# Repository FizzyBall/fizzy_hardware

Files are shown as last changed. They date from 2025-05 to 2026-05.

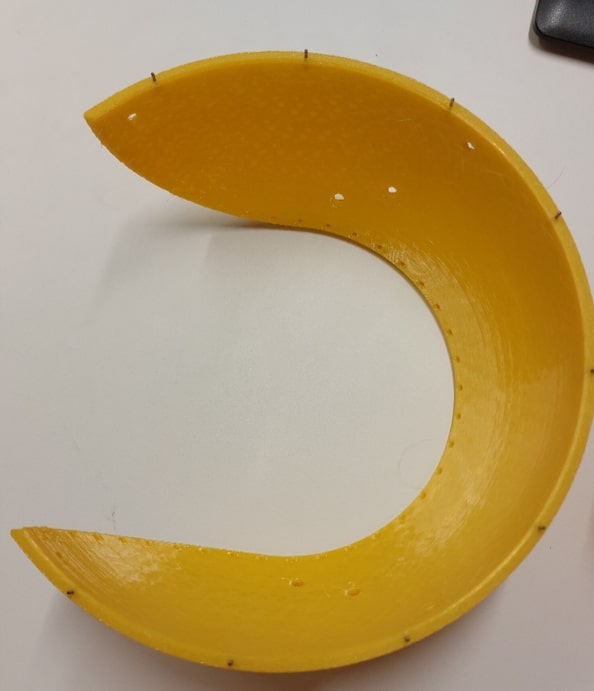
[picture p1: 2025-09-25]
Fizzy_BOM_pictures/image028.jpg

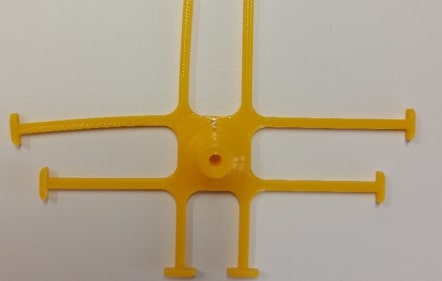
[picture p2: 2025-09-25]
Fizzy_BOM_pictures/image029.jpg

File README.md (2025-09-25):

# Hardware
Embodiment of the robotic ball

Assemblyv22-ezgif com-video-to-gif-converter

Drivetrain V3.0


Drivetrain V3.1


Rigid shell V1


Rigid shell V2


Flexible shell V1


Flexible shell V2


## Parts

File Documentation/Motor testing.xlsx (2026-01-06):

Requirements | min | max | unit | Setup | Voltage (V) | Stall torque (Nm) | Stall current (A) | Speed (RPM) | Mechanical power (W) | Electrical power (W) | Speed Counter Clockwise | No Load Current | Comments
Rotating Mass | 0.15 | 0.2 | kg | TS90M
Distance rotating mass to center of rotation | 0.035 | 0.045 | m | With PCB and battery | 5 | 0.22 | - | 114 | 1.29 | - | 112 | - | Speed with load 75 (clockwise) 67 (counterclockwise)
Torque to hold the drivetrain horizontal | 0.052 | 0.088 | Nm | With PCB and power supply | 5 | 0.20 | 1.2 | 115 | 1.20 | 6 | 109 | 0.356 | Motor directly on powersupply give 1,1A stall current (no motor driver)
Friction | 0.007 | 0.009 | Nm | Website specifications | 4.8 | - | - | 91 | - | - | - | - | Large difference between motors.
Minimal torque required | 0.059 | 0.097 | Nm | Website specifications | 6 | 0.19 | 0.9 | 111 | 1.10 | 5.4 | - | -
With safety factor 2 | 0.117 | 0.195 | Nm
With safety factor 4 | 0.234 | 0.389 | Nm | MG996R
Speed | 100 | 100 | RPM | With PCB and battery | 5 | 0.58 | - | 41 | 1.25 | - | 42 | -
Power required with safety 2 | 0.61 | 1.02 | W | With PCB and power supply | 5 | 0.39 | 0.67 | 40 | 0.82 | 3.35 | 42 | - | Could not supply the current draw, PCB dropout
Power required with safety 4 | 1.23 | 2.04 | W | Website specifications | 4.8 | 1.30 | - | 58 | 3.95 | - | - | -
Max power from PCB peak | 10 | 10 | W | Website specifications | 7.4 | 1.50 | 2.2 | 76 | 5.97 | 16.28 | - | -
 |  |  |  | N20 150RPM
 |  |  |  | Directly on power supply | 6 | - | 0.44 | 148 | - | 2.64 | - | -
 |  |  |  | Directly on power supply | 5 | 0.20 | 0.36 | 120 | 1.26 | 1.8 | - | 0.25
 |  |  |  | With DRV8833 motor driver and power supply | 5 | 0.13 | 0.22 | 115 | 0.76 | 1.1 | 116
 |  |  |  | With PCB and battery | 5 | 0.12 | - | 88 | 0.56 | - | 81 | - | Using motor driver from servo motor
 |  |  |  | With PCB and power supply | 5 | 0.12 | 0.4 | 93 | 0.57 | 2 | 86 | 0.25 | Using motor driver from servo motor
 |  |  |  | Website specifications | 6 | 0.17 | 0.55 | 150 | 1.34 | 3.3 | - | -
 |  |  |  | Only PCB no motor
 |  |  |  | With PCB and power supply | 5 |  |  |  |  |  |  | 0.2

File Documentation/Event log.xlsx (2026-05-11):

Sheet: Setup 1
 | PCB | Status | CFM |  | Bumper |  | Motor | O-ring |  | Suspension |  | Shell
 |  |  | Material | version | Material | version |  | Material | version | Material | version | Material | version | color | comments
 | IC69200A44F8 | assembled | TPU95A %80 infill | V1 35 mm | TPU95A 15% infill | V1 | TS90M1 | NBR 90 | 25 mm | x | x | x | x | x | x
Eventlog | Date | Event
 | 2025-12-29 | Testing for 30 min full speed
 |  | No effect seen
 | 2026-01-21 | Assembled in Yellow ball (baseball design) |  |  |  |  |  |  |  | TPU95A polymaker 15% infill | V1 | TPU95A polymaker 15% infill | V1 | Yellow | Baseball design with two screws for easy acces
 | 2026-01-21 | Tested at BSO location. Children kicked the ball hard -> no imidiate damage reported - connection los when kicked hard - cause unknown
 | 2026-02-11 | Highlight Delft (4 days)
 | 2026-02-11 | battery was drained to 40% after 5 hours of use after day one
 | 2026-02-12 | battery was drained to ~40% after 5 hours of use after day one
 | 2026-04-02 | motor-axis connection got loose. Locktide or instant glue was not working properly.
 | 2026-04-09 | took apart the drivetrain. Only one 4mm and 3mm bearing left and no fixed axis
 | may + june | Used By the BEP group to test and read out IMU data

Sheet: Setup 2
 | PCB | Status | CFM |  | Bumper |  | Motor | O-ring |  | Suspension |  | Shell
 |  |  | Material | version | Material | version |  | Material | version | Material | version | Material | version | comments
 | IC69200A4F78 | assembled | x | x | x | x | x | x | x | x | x | x | x | x
Eventlog | Date | Event
 | 2026-02-10 | assembled for highlight delft | TPC 40D green | V1 35 mm | TPC 40D green | V1 | TS90M2 | NBR 90 | 24 mm | TPC 40D green | with inside connection | TPC 40D green | Soccerball | Printed in two parts
 | 2026-02-11 | Highlight Delft (4 days)
 |  | battery was drained to ~40% after 5 hours of use after day one
 | 2026-02-12 | 30% battery left. Did see a bit more connection lost, could not figure out why.
 | months may through june | Used by BEP group for classification
 | 2026-05-02 | Added a washer to the battery, for better clamping force

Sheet: Setup 3
 | PCB | Status | CFM |  | Bumper |  | Motor | O-ring |  | Suspension |  | Shell
 |  |  | Material | version | Material | version |  | Material | version | Material | version | Material | version | color | comments
NEW from aachen | 1C69200A4F58 | assembled | x | x | x | x | x | x | x | x | x | x | x | x | x
Eventlog | Date | Event
 | 2026-02-06 | Arrived from Aachen to use as backup
 | 2026-02-12 | assembled with CFM and battery | TPC 40D red | V1 35 mm | TPC 40D red | V1 | TS90M3 | NBR 90 | 24 mm | TPU95A Black | old one through the shell | TPU95A Black | old | Black | Used as demo
 |  | used as backup for highlight delft
 | 2026-04-09 | rebuild new version for soccerball design |  |  |  |  |  |  | 23 mm | polymaker TPU 90A | with inside connection | polymaker TPU 90A | Soccerball | Teal | printed in 2 parts
 | 2026-05-11 | Lend version to bachelor student Twente, added a washer, changed the o-ring |  |  |  |  |  |  | 22 mm?

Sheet: Setup 4
 | PCB | Status | CFM |  | Bumper |  | Motor | O-ring |  | Suspension |  | Shell
 |  |  | Material | version | Material | version |  | Material | version | Material | version | Material | version | color | comments
 | IC69200A4F64 | assembled | TPU95A %80 infill | V1 35 mm | TPU95A 15% infill | V1 | TS90M4 | NBR 90 | 25 mm | TPU95A %80 infill | V1 | TPU95A 15% infill | V1 | Black | One wall on the inside
Eventlog | Date | Event
 | 2025-09-01 | Given to Product now studio course
 | 2026-02-12 | Returned from Product now studio course Broken motor connector on the pcb Students fixed it by adding wires and soldering them to the PCB at other points Taken out of the black shell and used the bearings for setup 3
 | 2026-04-02 | replaced the drivetrain in the yellow ball. Also took the bumper from the setup 1 and the extra brass weights. |  |  |  |  |  |  |  | TPU95A polymaker 15% infill | V1 | TPU95A polymaker 15% infill | V1 | Yellow | Baseball design with two screws for easy acces

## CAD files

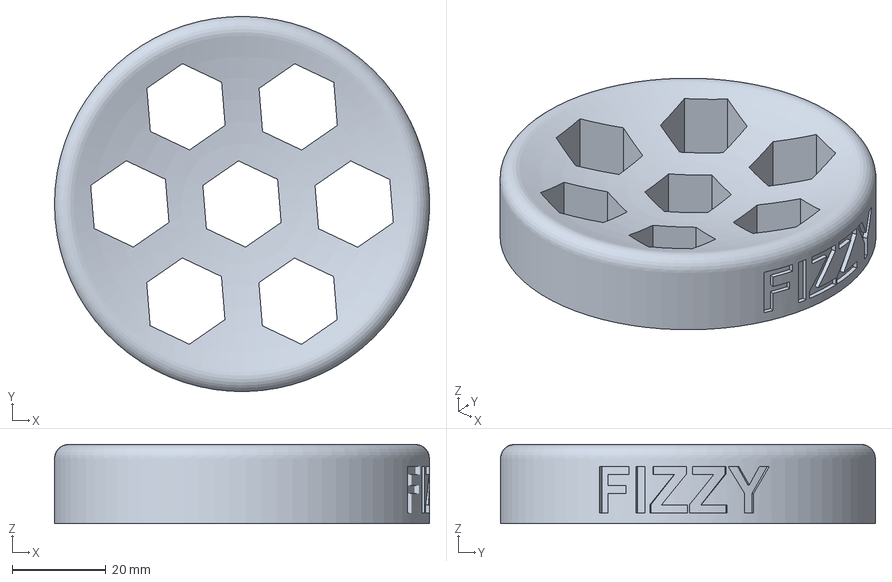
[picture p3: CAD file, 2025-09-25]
STL files/Fizzy_stand_v1 v1.3mf
80.0 x 80.0 x 16.9 mm

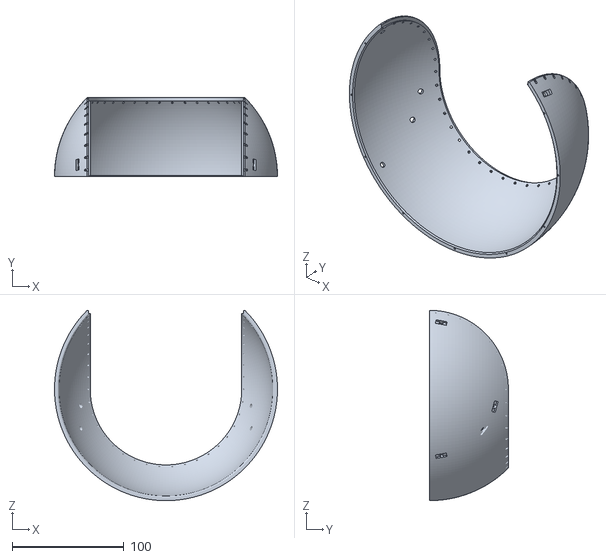
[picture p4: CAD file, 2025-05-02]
STL files/Shell/green right.stl
200.0 x 70.7 x 170.6

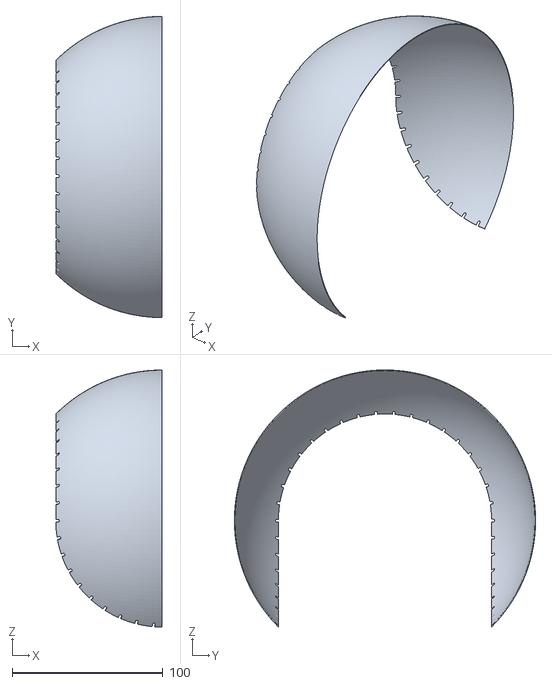
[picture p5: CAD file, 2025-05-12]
STL files/Shell/Modifiers fuzzy skin/blue left fuzzy.stl
70.7 x 200.0 x 170.6

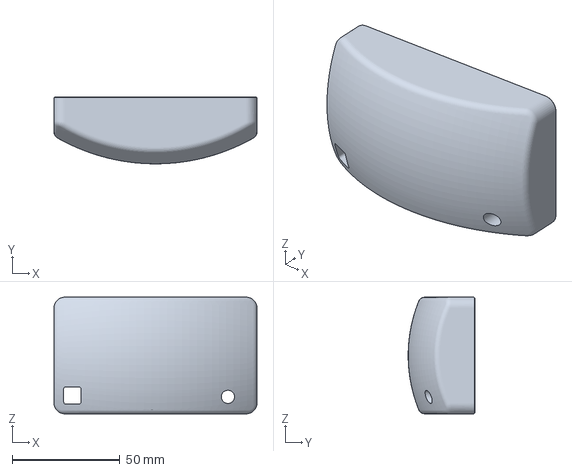
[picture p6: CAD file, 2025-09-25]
STL files/Bumper.3mf
94.0 x 30.9 x 54.0 mm

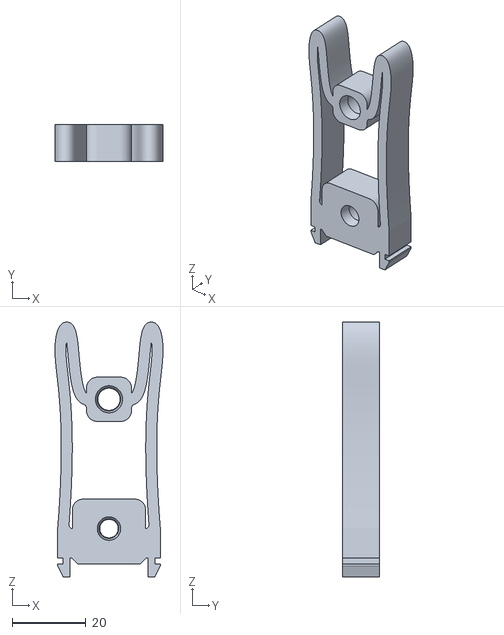
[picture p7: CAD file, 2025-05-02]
STL files/CFM snapfit 35 mm.stl
29.2 x 10.0 x 69.0

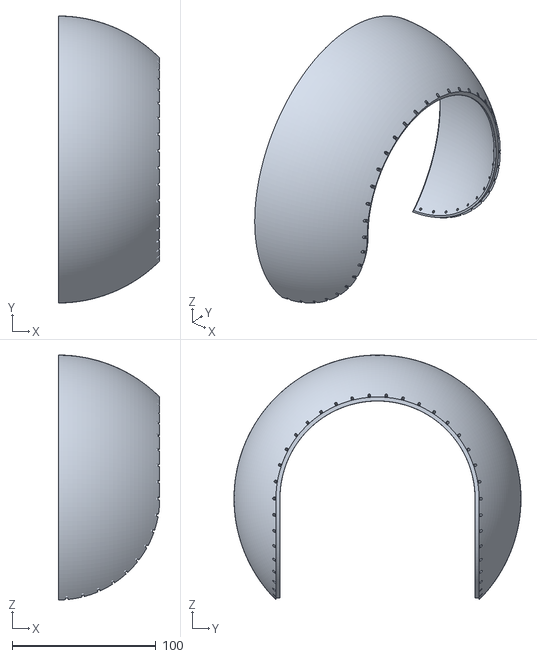
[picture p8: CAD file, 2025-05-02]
STL files/Shell/blue left.stl
70.7 x 200.0 x 170.6

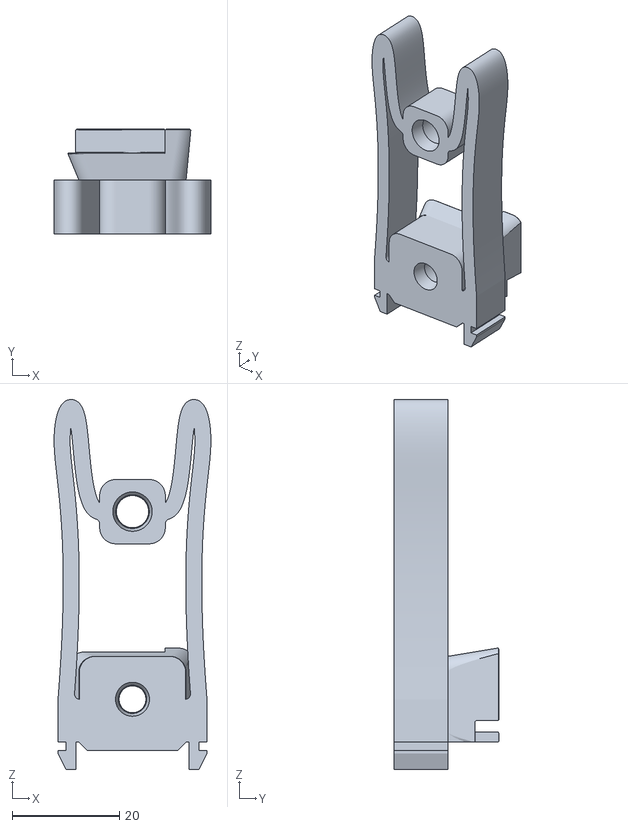
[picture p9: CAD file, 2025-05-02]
STL files/CFM snapfit 35 mm motor connection v1.stl
29.2 x 19.5 x 69.0

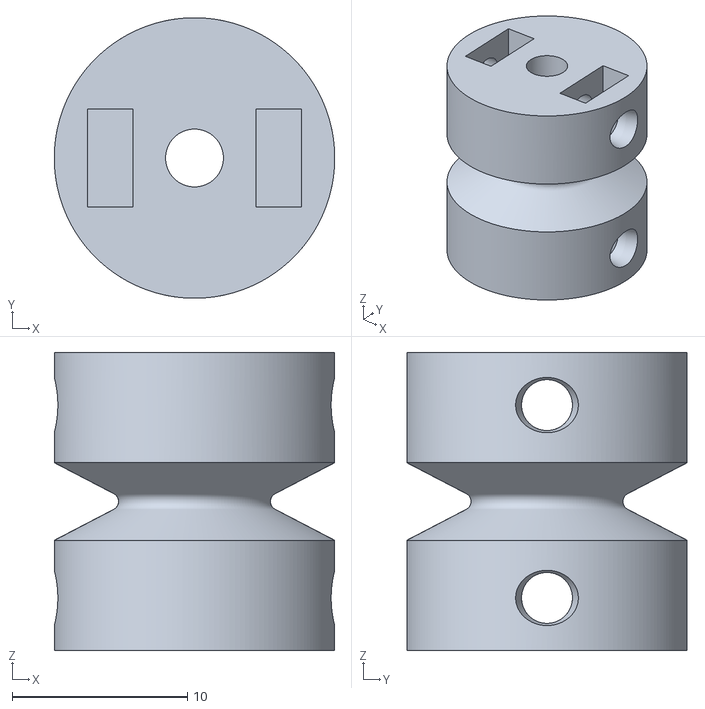
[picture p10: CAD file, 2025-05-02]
STL files/pulley v shape 55 deg v1.stl
16.0 x 16.0 x 17.0

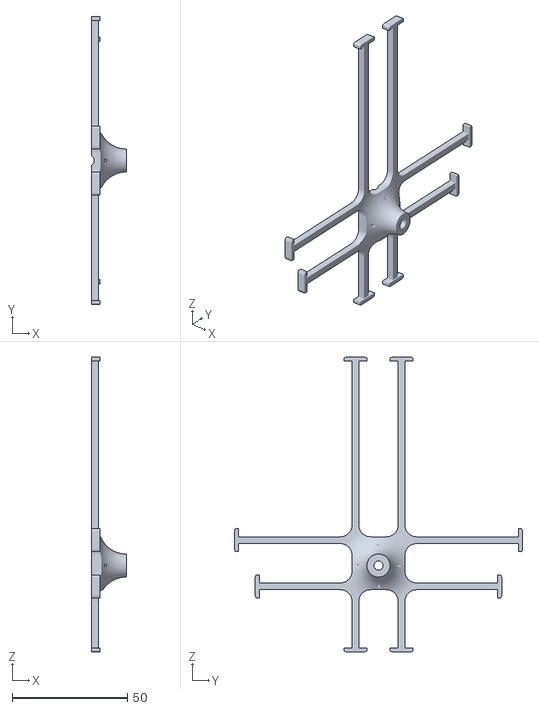
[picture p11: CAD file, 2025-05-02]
STL files/Hub v3.stl
15.0 x 125.0 x 128.0

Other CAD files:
STL files/Shell/green left.stl
STL files/Shell/Modifiers fuzzy skin/green left fuzzy.stl
STL files/Shell/Modifiers fuzzy skin/green right fuzzy.stl
STL files/Shell/Modifiers fuzzy skin/blue right fuzzy.stl
STL files/pulley v shape 55 deg 4mm axis v2.stl

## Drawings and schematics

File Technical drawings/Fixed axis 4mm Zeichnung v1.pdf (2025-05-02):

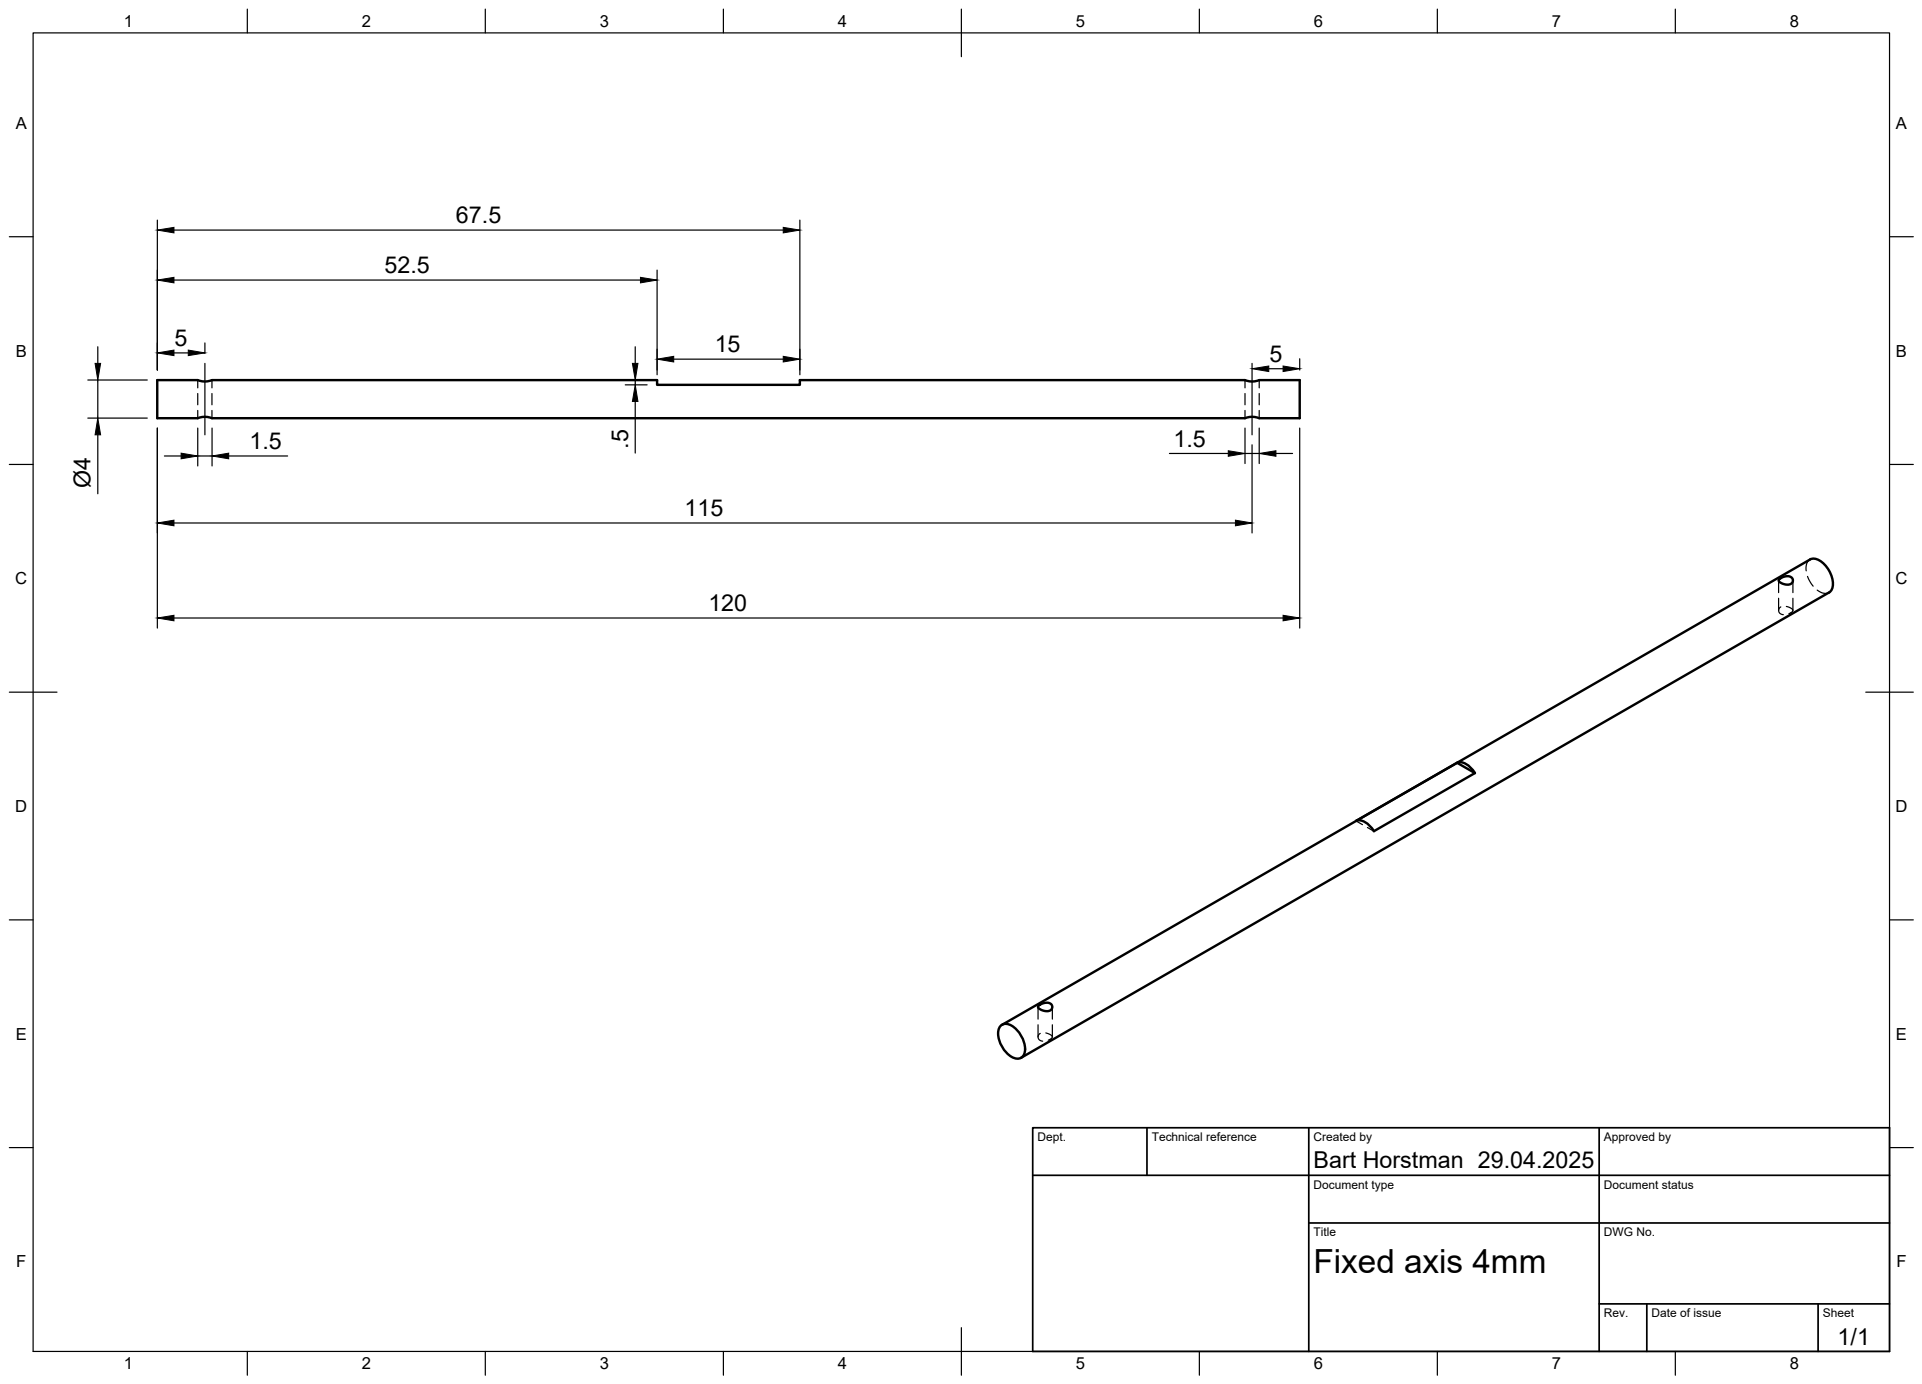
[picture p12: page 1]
Title; DWG No.; Rev.; Date of issue; Sheet; Fixed axis 4mm

Dept. | Technical reference | Created by Bart Horstman 29.04.2025 | Approved by

Document type | Document status

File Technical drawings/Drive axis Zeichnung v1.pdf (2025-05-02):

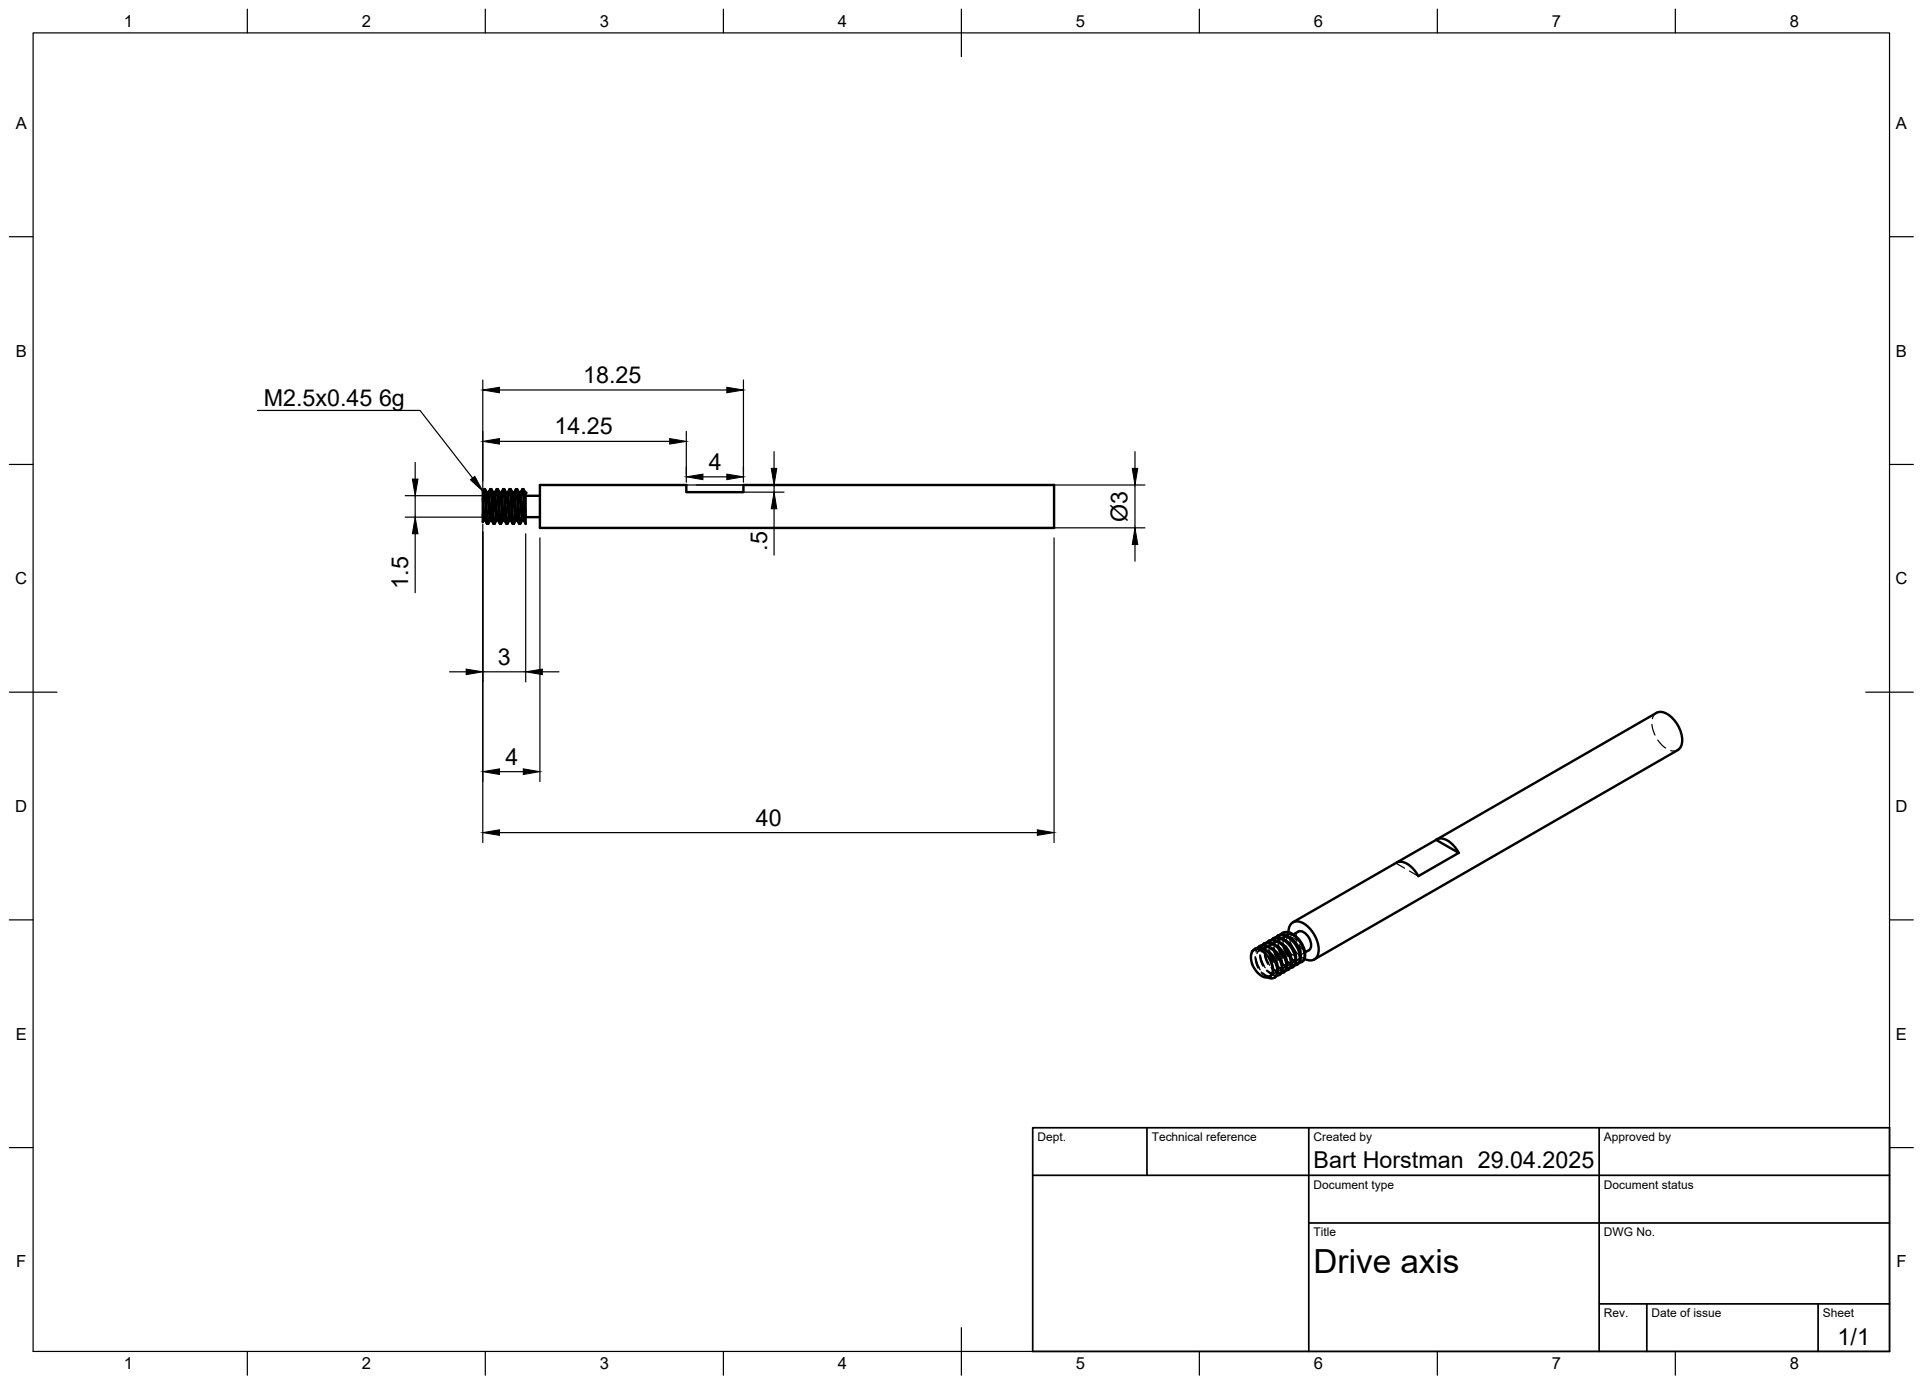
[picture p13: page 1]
Title; DWG No.; Rev.; Date of issue; Sheet; Drive axis

Dept. | Technical reference | Created by Bart Horstman 29.04.2025 | Approved by

Document type | Document status

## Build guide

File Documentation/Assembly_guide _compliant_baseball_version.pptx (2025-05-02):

## Assembly Guide Compliant Baseball Version

## Improvements

- Test out different materials
  - TPC more elastic less damping
  - TPU90A or TPU85A less dense material, so lighter but less stiff
  - TPE ??
  - VarioShore can change the density and with that change the stiffness
- All of them need proper tuning of the print settings in order to print well

## Manufacturing

- Follow the technical drawings
- The drive axis can be made on a lathe
- The fixed axis can be done on a milling machine or by hand with some additional aiding pieces to drill in a round bar

- Making the axes

## Manufacturing

- See print settings for PLA

- Infill rate is 15%
- You can print two at the same time
- Support can be added to make the v-shape better
  - Best if dissolvable support is used

- Print settings

- Printing the pulleys

## Manufacturing

- See print settings for TPU 95A

- Infill rate is 80%
- You can print two at the same time
- No support needed

- Print settings

- Printing the CFM

## Manufacturing

- See TPU print settings

- Infill rate is 15%
- Add support for the top part

- Print settings

- Printing the Bumper

## Manufacturing

- See print settings for TPU 95A

- Infill rate is 15%
- You can print two at the same time
- Printed with 1 wall thickness
- Used fuzzy skin to increase the wall thickness on the outside (Use the modifiers in the print file)
- Add instruction on how to add the Fuzzy skin

- Print settings

- Printing the shell

## Manufacturing

- See TPU print settings

- Infill rate is 15%
- You can print two at the same time (depending on the bed size)
- No support needed

- Print settings

- Printing the suspension

## Assembly

- Assembly Drivetrain

1. Solder all the components on the PCB, except for the battery holder
2. Adjust the cable of the servo motor to fit the connector on the PCB
3. Modify one of the asseccories of the servo motor to be used to tighten the drive axis on the motor
4. Add a little bit of loctide or instant glue to the drive axis thread and attach the drive axis to the motor
5. Insert the bearings in the CFMs
  1. Small bearings at the motor
  2. Large bearings at the fixed axis

1. Snap the CFMs in the PCB
  1. Make sure it is orientated in the right way
2. Insert the battery holder and solder it in possition
3. Insert the nut and set screw to both pulleys
4. Insert the motor with axis through the bearings and make sure to place the pulley and belt in between the CFMs
5. Insert a screw to attach the motor to the CFM
6. Tighten the set screw in the pulley with a little bit of loctide
7. Add the bumper
8. Insert fixed axis through the CFMs with the pulley and belt in between
9. Tighten the pulley again with a little bit of loctide on the setscrew

## Assembly

1. Put alignment pins in one half
2. Glue shells together with flexible glue, make sure the two halves align
  1. Don’t use to much glue, hazing will occur (turning white), and the glue will prevent proper welding of the two halves later
  2. Glue it only to keep it in place for the welding part
3. Let the glue dry (at least an hour)
4. Prepare the welding of the two halves
5. Weld
6. Let it cool down (at least an hours)

- Assembly Half shells

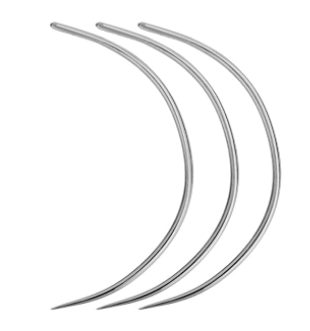
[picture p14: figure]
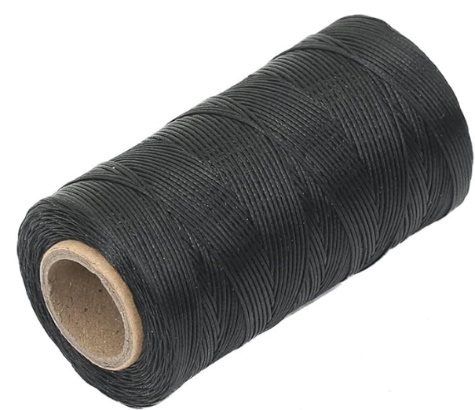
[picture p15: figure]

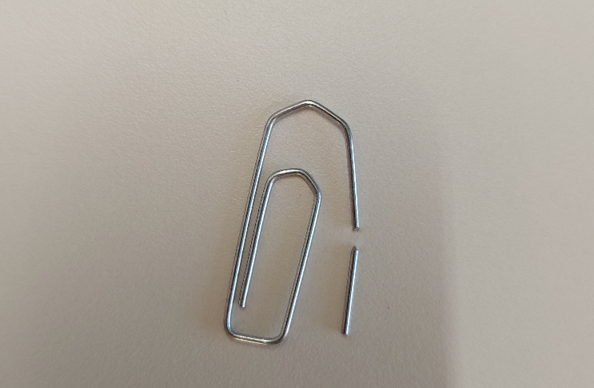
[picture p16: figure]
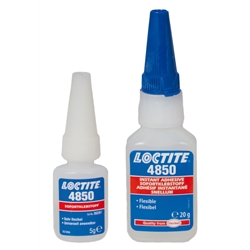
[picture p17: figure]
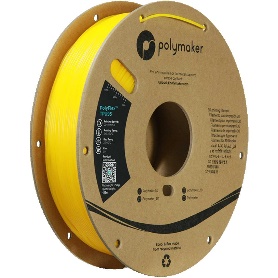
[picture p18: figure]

## Assembly

- Assembly Suspension

1. Insert the suspension hubs in the shell. Do this by press fitting it through like in the picture

## Assembly

- Assembly Whole ball

1. Start stitching the first half of the ball
2. Connect the suspension hubs to the fixed axis with the drivetrain in the middle
  1. Use the pins to do so
3. Finish the stitching of the rest of the ball

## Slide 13

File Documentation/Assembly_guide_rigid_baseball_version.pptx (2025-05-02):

## Assembly Guide Rigid Baseball Version

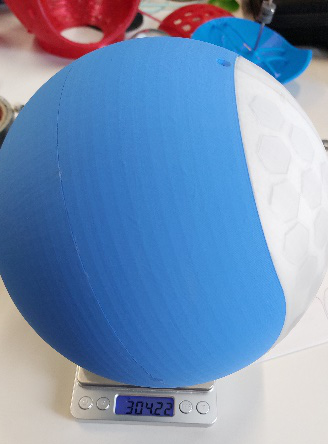
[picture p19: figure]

Material | PLA
Shell design | Baseball
Weight including suspension | 304g
Wall thickness | 3mm
Infill | 15%
Connection method | Screws

## Improvements

- Move location of the hole as indicated in the picture, to avoid splitting the two transparent shells. Same for the hole on the other side.
- Add countermasses to the shell and print them with the shell

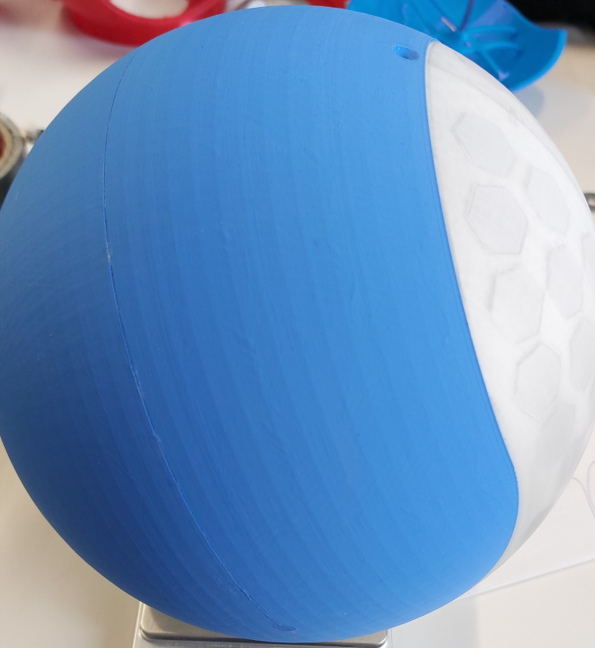
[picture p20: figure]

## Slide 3

- See print settings for PLA
- Infill rate is 15%
- Used tree support for best results with overhang
- You can print two at the time

- Print settings

- Printing the shell

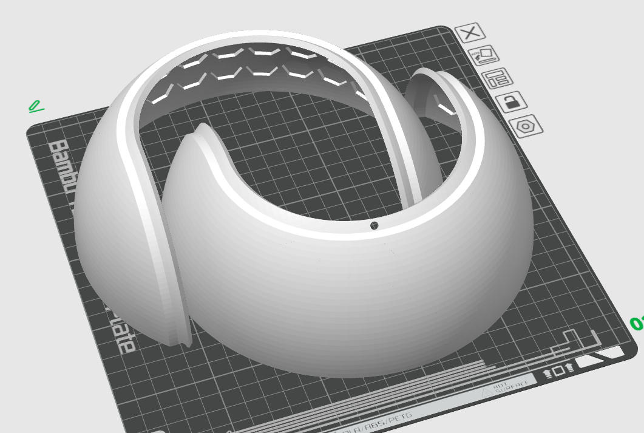
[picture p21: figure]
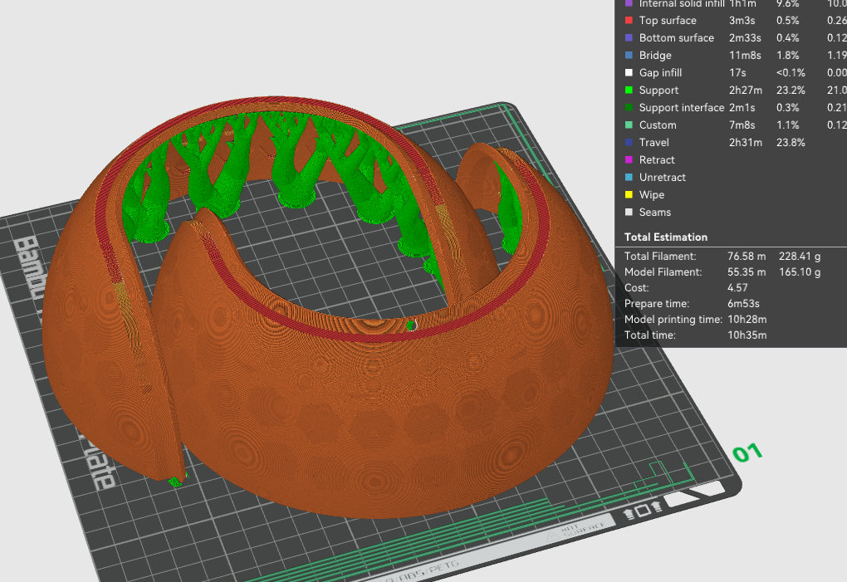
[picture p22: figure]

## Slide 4

- See PLA and TPU print settings
- Print bending parts on their sides for most strength

- Bending parts (red) out of TPU
- Connection to shell and connection to axis out of PLA

- Print settings

- Printing the suspension

PLA

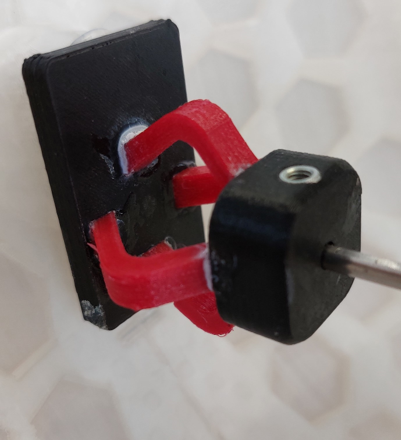
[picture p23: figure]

TPU

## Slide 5

- M3 10mm (length including the head)
- Loctite 406 instant glue
- M3 Inserts
1. Put alignment pins in one half
2. Glue shells together
3. Melt inserts in bottom shell

- Assembly shell

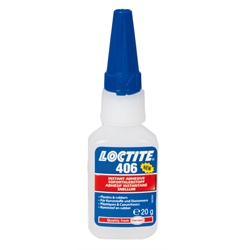
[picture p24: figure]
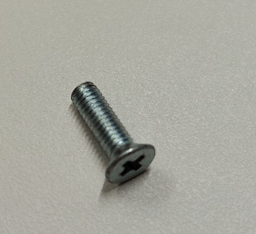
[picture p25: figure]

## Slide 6

- Assembly suspension

- Glue in bending parts with instant glue or flexible glue
  - Make sure to have the insert part facing upwards like in the picture. Otherwise fixating the axis is harder
- Glue the whole suspension in the shell with the hot glue gun
  - This allows you to take it out if needed, but stays in place for general use

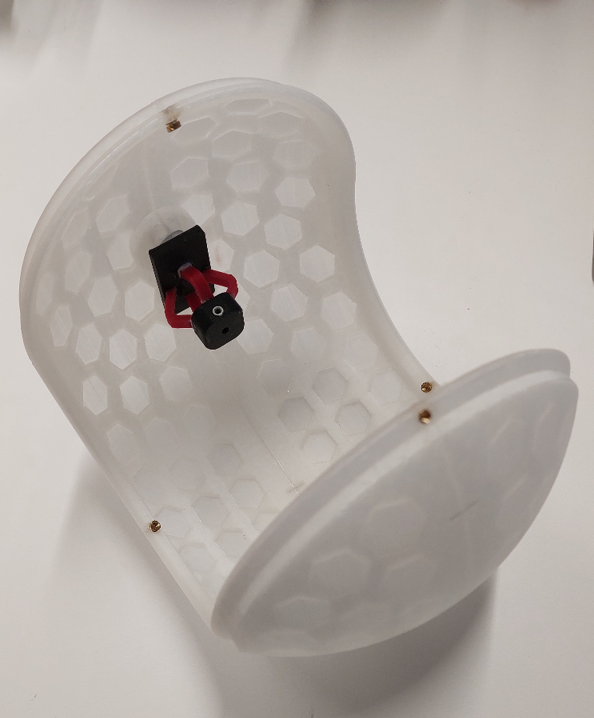
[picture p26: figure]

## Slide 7

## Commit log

2025-05-12 modifier change
    [blue left fuzzy.stl, blue right fuzzy.stl, green left fuzzy.stl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]
2025-05-12 added components to the BOM
2025-06-02 commit new BOM list
2025-09-25 Added picture folder for easy upload to website
    [Bumper.3mf, Bumper.stl, Bumper_old.stl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]
2025-10-13 changed the location of some printing files for the components + added the assembly step file
    [Bumper_old.stl, Bumper_prusa.3mf, CFM snapfit motor connection.stl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]
2025-10-13 same as previous commit
    [blue right with fuzzy skinn (prusa).3mf, green left (new filament).3mf, green left.3mf]
2025-11-14 added order list as a tab
    [Fizzy_BOM.xlsx]
2026-01-06 fizzy_bom change
    [Fizzy_BOM.xlsx]
2026-03-04 changed event log
    [Event log.xlsx]
